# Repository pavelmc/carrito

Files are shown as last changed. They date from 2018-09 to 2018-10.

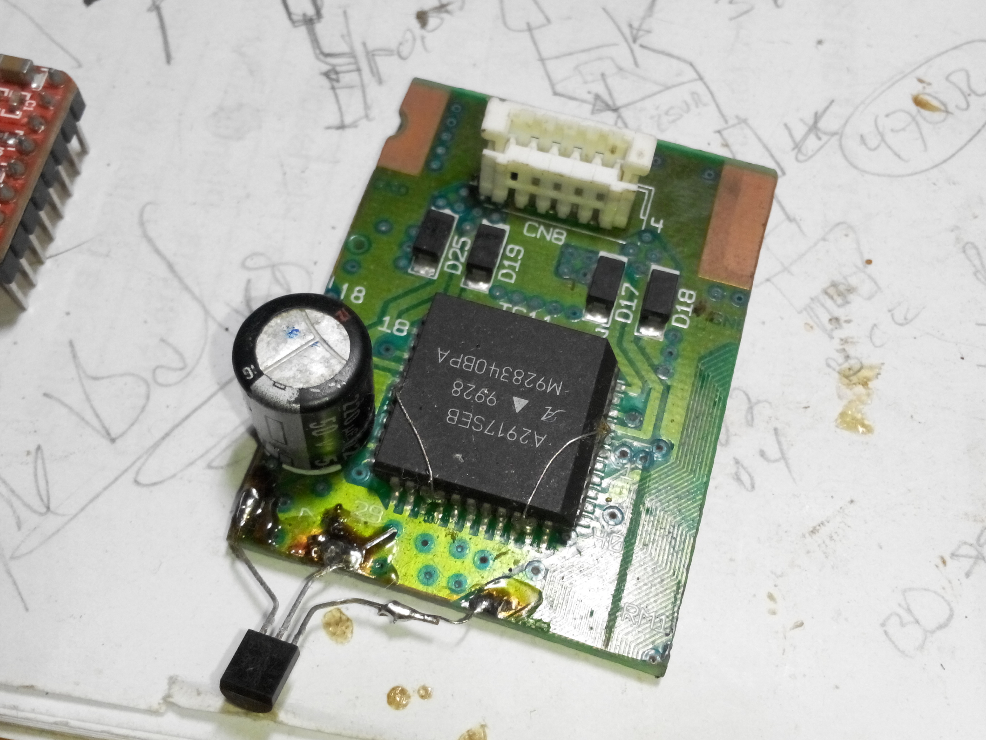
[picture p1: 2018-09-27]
photos/allegro-controller-death.jpg

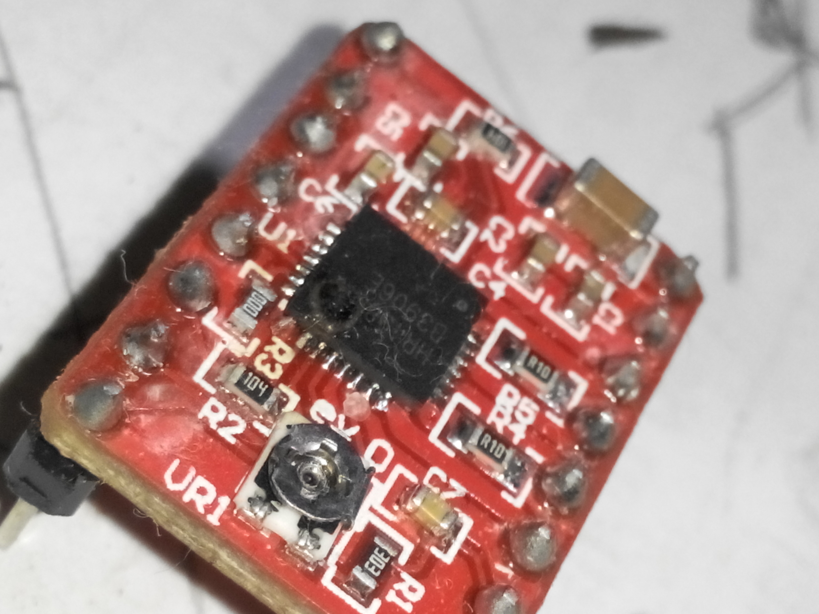
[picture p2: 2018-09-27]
photos/pololu-controller-death.jpg

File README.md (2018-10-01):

# Carrito (Spanish for Small car) #



This is a homebrewed small car powered by Arduino, there is no particular blueprint for it, the parts comes and go to fit my needs, this evolves continually. Almost all parts were scraped from my junkbox.

You can take a peek at the (always evolving) fritzing file in the "extra" directory (there is also PNG and PDF versions for your convenience)

The main motivations to make this car is the fact that I haven't a cool Arduino project to display... I also confess that I didn't had a remote controlled car as a child so I made this to my children also.

# Dependencies #

If you want to build or test this you will need a few extra things not in this repository:

* The [remote control](https://github.com/pavelmc/carrito-control) device to command this thing.
* A custom lib to command the stepper motor, its called [stepperUnipolar](https://github.com/pavelmc/stepperUnipolar) and has some nice features.
* A library to control the nRF24l01 device, I use the nRFLite lib, you can find it on the Arduino IDE Library manager.

# Actual Hardware #

**Power source:** Laptop batteries; I have become a recycle fan of laptop batteries on any kind for many uses, I have it from 1.2Ah to 2.5Ah, in this case I chose 4 cells is 2P2S mode of 2.2Ah, that gives a total of 6.0 to 8.4 V at up to 4.4 Ah, that's plenty of power for the task.

Every lipo battery need a [BMS](wikipedia:battery_monitor_system) and I borrowed one controller from a Baofeng handheld radio battery pack, it was rated 1.800mAh (1,8Ah) but carefully inspection showed that the MOSFET on the BMS was capable of handling up to 10 amps, so it must be up to the task. (I calculate a peak load of 1.3 Amps top)

_note:_ I charged the battery pack at the design stage and after about a month of bench and field test (about 3 to 4 days per week of tests with ~1 hour per day) it's now at ~7.0 V about 50% of charge; maximum current measured was about 1.8A, nice very nice.

**Motion drive:** Old dotmatrix Epson Printer DC motor and gears commanded by a 6AM14 mosfet Bridge that allows to control the direction (polarity inversion) and speed (via a PWM on a P-channel MOSFET)

**Direction control:** Stepper motor controlling a gear that rotates the front wheels. The motor was borrowed from a old dotmatrix Epson Printer. The motor is unipolar (type 17PM-K303, NEMA17 equivalent from Minebea) controlled by 4 MOSFET borrowed from a PC Motherboard (P75N02, 7.5 milli Ohms and 25 Volt) directly connected to the 74HC595 at 0-3.3V logic.

The motor ratings specs 1.2A on the coil and max of 3.0 Volts, so I fit a positive side current limiter using a PNP darlingtown transistor circuit (2SA1568, again borrowed from the printer, this are the pin controllers on the datMatrix printer)

**Direction artifacts:** The front wheels direction has one problem: it can move and miss steps on bumps and hits, so I need some way to know the position, but all time position are good or only a few ones? powering the stepper is a way to keep the direction in place, but that monster eating 1.2 Amp is not an option.

After analyze the situation I found that I will only need three position reports:

* Full left.
* Mid of front facing.
* Full right.

Left/Right limits was implemented with mouse click switches and also served as hardware limiters, the front facing position as a little tricky (I tried some dancing switches from an old bubblejet printer and other options).

I ended with an Hall effect sensor, it has A42E label but I can't find the datasheet _(if you know what part it's I will appreciate any clue, the initial "A" letter seems like the Allegro one)_, it was borrowed from an old floppy disk drive, per the circuit I can tell that it needs a pull up 10k transistor for 5V and of curse the pinout is evident.



This hall sensor triggers a pin low once the direction is facing forward, as simple as that. The pull up is by software on the arduino programming, test proved that it works just fine on 3.3V.

**Remote control:** the remote control is designed/made from day one using a pair of nRF24L01 modules at 250 kbps, more than the needed for the task. I tested a lot of libs for this modules and ended using the nrflite one by his final small size firmware and easy programming.

# No Go Hardware & Failed tries #

This is a list of failed tries of hardware and ideas and his explanation (you can find images of the items described here in the folder no-go-and-failures)

## Power inversion for the power motor ##

First try was using 12V Relays from a UPS, it consumes only 28mA to drive the coil and can handle up to 10A, driver circuit is just a transistor connected to the Arduino, so it was a nice idea, but not in practice.



Theory some times is ridiculously killed by practice: the 8.4V of power was just enough to activate the 12V relays, but once the voltage of the battery dropped to ~7V it's stops of activate the relays, or activates only one... so no-go on this.

Next obvious solution was a H-Bridge, but P MOSFET transistor are rate here, so I surfed the net and found some clever design using power bipolar transistors and even darlingtons NPN-PNP pairs... hummm printers have that...



Yes, I have them PNP 2SA1568 and NPN 2SD2131, so hands to the bech... the result was a bulk & spider wired H bridge on a large heatsink from a PC power supply, it worked well but also dissipated some heat, losses was about 0.3V on PNP and 0.25V on the NPN side, that at ~700 mA, loses was about half a watt on heat, not bad in paper but the "finger test" was no so, it feels uncomfortably hot at touch.

So big and hot, yet I need a PNP transistor to control the +Vcc with the PWM of the Arduino so more bulk and heat, no thanks... I need another solution.

"Only archives a goal who seek and work for it", tells a Spanish old saying. Searching on the junk box I found a old and dust power chip with his original heatsink: 6AM14 Bingo!

That is just 3 pairs of N and P channel matched MOSFETS (7 Amps One and a half H-bridge) so I can wire the H-bridge and the remaining P-channel mosfet to control the PWM, results: under 1mA on standby and losses are under 100mW on work at 1A (no perceptible warm on full power drive), Wow MOSFET RULEZ!!!

## Too big power motor: ##



I prepared the chassis to hold a power motor that is just too big to power this little monster, it eat around 1A at 8.4V and can develop a lot of speed, in the first tries I realized that and discarded it in favor of a motor half the size of that; now it eats 600mA (0.6A) at full power and plenty of speed and power for the task

## Direction Stepper motor to small ##



I build the direction mechanism like an old car, moving the entire front wheels support and not each front wheel at a time in opposite direction (like any modern car). But tests showed that the selected motor (no branding or data, just a unipolar stepper motor of 200 steps per turn, see picture) was not enough for the task at least at 6-8V of power supply with current limiting.

I then moved to another stepper motor bigger and it happens to has a gear that is the same tooth pace that the main gear, this motor was from a Epson printer (is states in the chassis: EM-242) and its of bipolar type.

## Direction stepper motor controller death ##



When I selected the above mentioned bipolar stepper motor I realize that I don't have a bipolar controller, then turned into the printer where it was borrowed and spotted a Allegro controller for it (A2917SEB) I get a hand saw and cut the PCB and by the datasheet I make it and get some code to get it to work.

Early test showed that the main Vcc of the motor was not enough for the task (it works on a +35V Vcc system and I have 6.0 to 8.4V from lipo batteries) I think on ways to increase the power adding more batteries up to 9.0 to 12.6V but that will nedd a BMS of three batteries and I have only 2S BMS at hand.

Testing other tricks I made a wrong connection and... it stopped working: R.I.P. A2917SEB. :(

## Direction stepper motor controller death (yes, the second one) ##

Then I was forced to buy a controller, in the cuban market this is hard but fortunately I found a friend that has a A4899 Pololu controller available, just great!

Buy, mount, test: OK. It works flawlessly, on the test bench. Now it's time to put it on the real hardware... fail... what's wrong? Simple: I switched the motor power (8.4V) with the digital power (max 5.5V)... results: Pololu controller is death, you can see the burn blob on the IC.



Miraculously the Arduino Pro Mini survived!, it received the +8.4V (capable of 4.4 Amps!) and did not die... thanks to the luck I had the nRF24 module disconnected from the Arduino...

This lead to discard the mentioned bipolar motor (I'm mad at bipolar motors... GGGRRR) and switch to the actual unipolar motor with a combination of Mosfets switching the motor coils to ground and a PNP bipolar transistor as current source (1.2 A as per the motor datasheet)

The motor was again borrowed from the same printer, (MINEBEA or MNB brand, type 17PM-K303, and equivalent of a NEMA17 one) datasheet specs are 1.2A current and max 3.0V so my 6.0-8.4V is enough.

## Not enough input/output pins, the case of the 74HC595 ##

At some point I realized that I will have not enough input/output pins, and realizing that I have the hardware SPI bus on use I it to command a 74HC595 shift register.

Then I realize that I will need a way to move the motor pins to the shift register, there is some examples out there, even adafruit has a shield based on that idea, but I can find a lib to make this... so...

I crafted a unipolar stepper lib to address simple pins handling or returning the pin values to pass to a shift register like the 74HC595, you can find it here [stepperunipolar](http://github.com/pavelmc/stepperunipolar) it is on a dev stage, it need a lot of work on the examples and docs to get ready for the public domain, so use it at your own risk.

Still in construction, check back later.

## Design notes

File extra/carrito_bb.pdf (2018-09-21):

6.0v to 8.4V From a
2P2S Lithium Ion
Battery with a
proper BMS

This is a basic Current Source to feed the Stepper motor, in this case 1.2 Amps aprox.

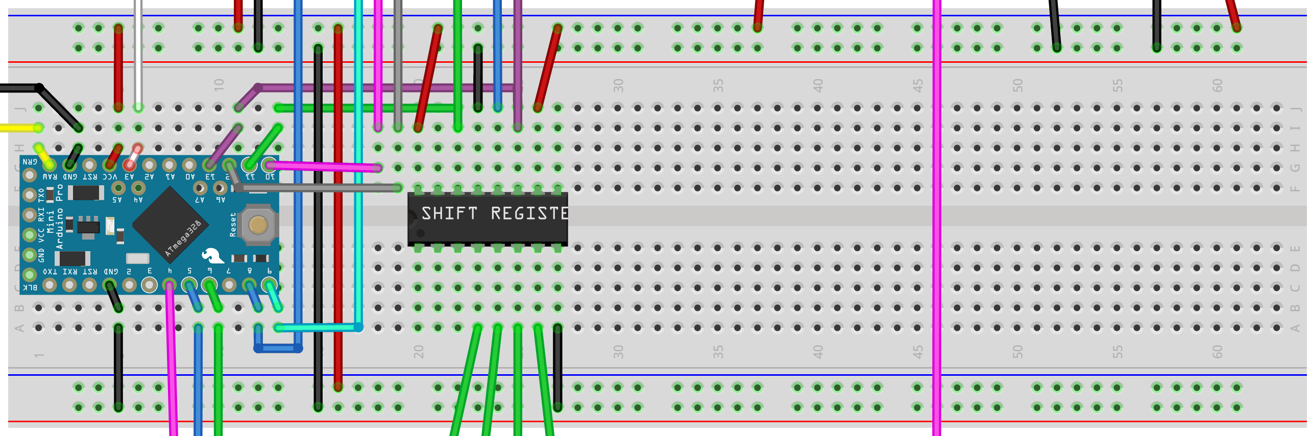
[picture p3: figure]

A Heat Sink is mandatory

Power Transistor is 2SA1568 Lower Power one is 2N3906

This is the motor that turns the front wheels. It's a NEMA17 like 3V@1.2A Unipolar one. Brand is MINEBEA (MNB)

Al 4 N-channel MosFET
are PL06N03 SMD ones
nRF24L01 Module | Two momentary limit switch (the positive feed is the one at the right, the negative feeded is at left)
| One Hall sensor to sign we are facing ahead (it's pulled down when magnet is on position, high the rest of the time)

H-bridge connector + Speed control.

The function is as follow:
* Pin 5 controls the car
movement direction (low
forward, hig reverse)

* Pin 6 is a PWM control of the speed of the movement (with a P-channel MosFET) 0 is no movement and 255 is full
power, Positive going PWM.

Carrito: A remote controlled car from parts in my junkbox =================================================

Author: Pavel Milanes (CO7WT)
E-mail: pavelmc@gmail.com
Web: https://github.com/pavelmc/carrito

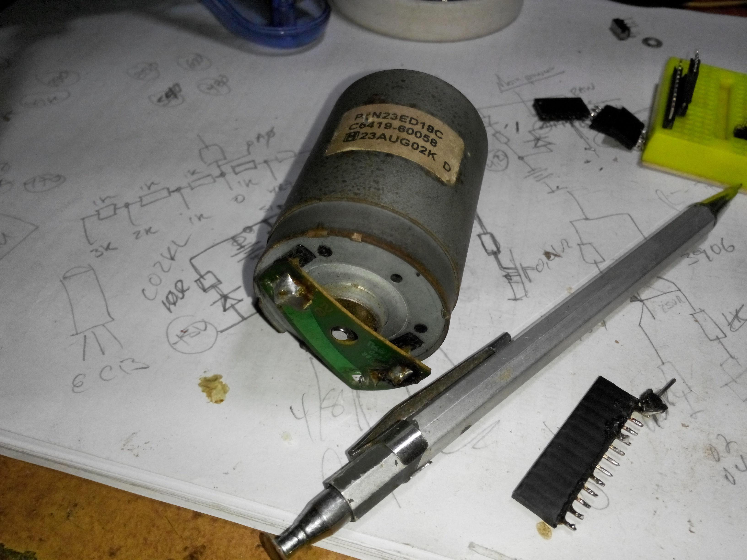
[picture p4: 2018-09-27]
photos/big-motor.jpg

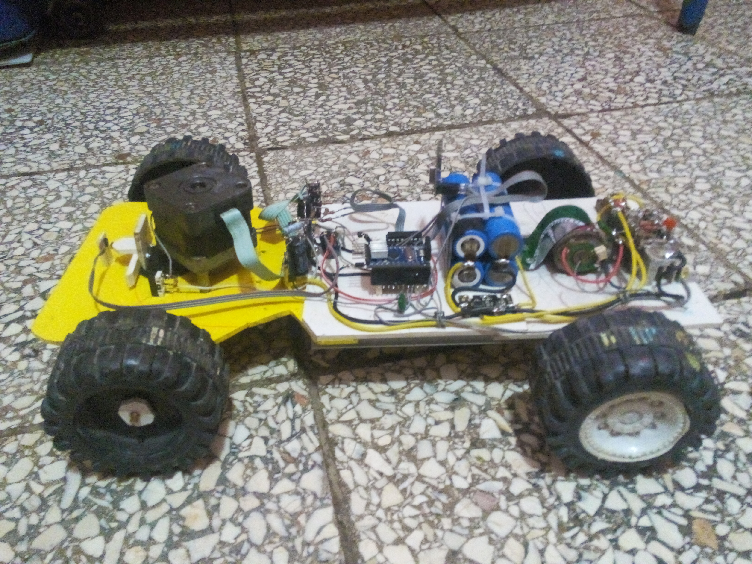
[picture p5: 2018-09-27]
photos/bare-bones-car.jpg

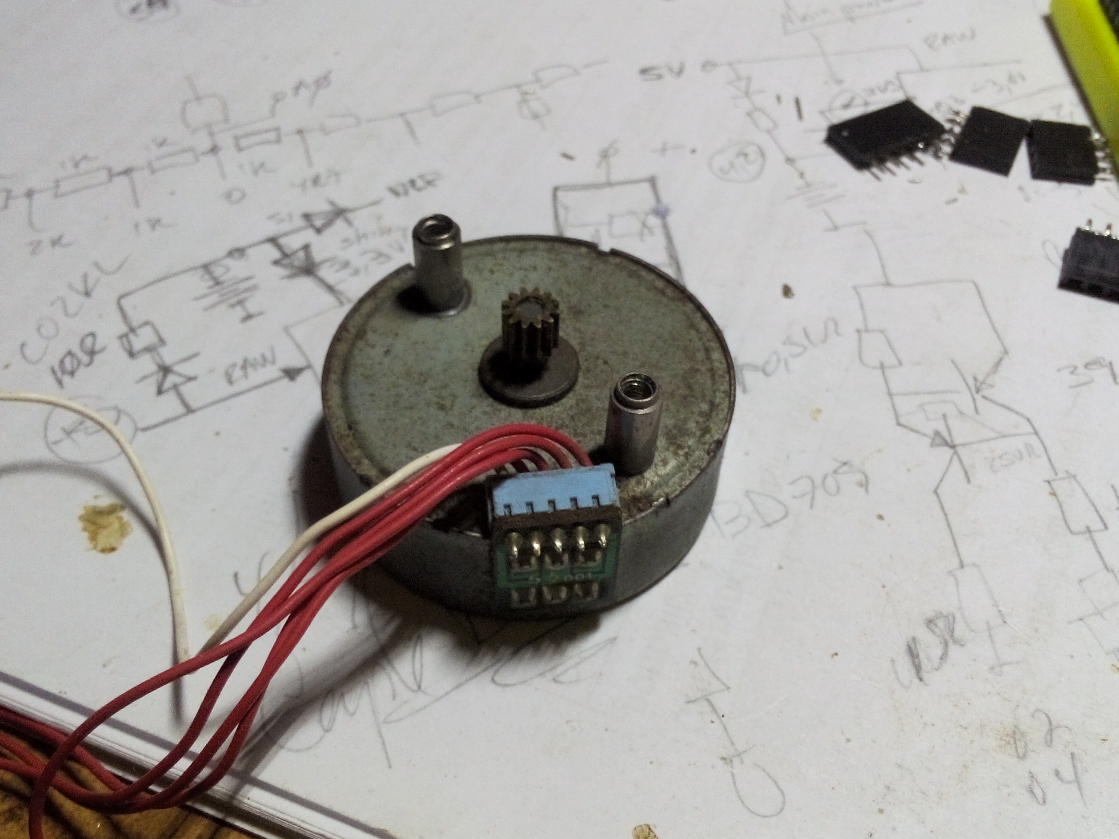
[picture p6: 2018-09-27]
photos/small-stepper-motor.jpg

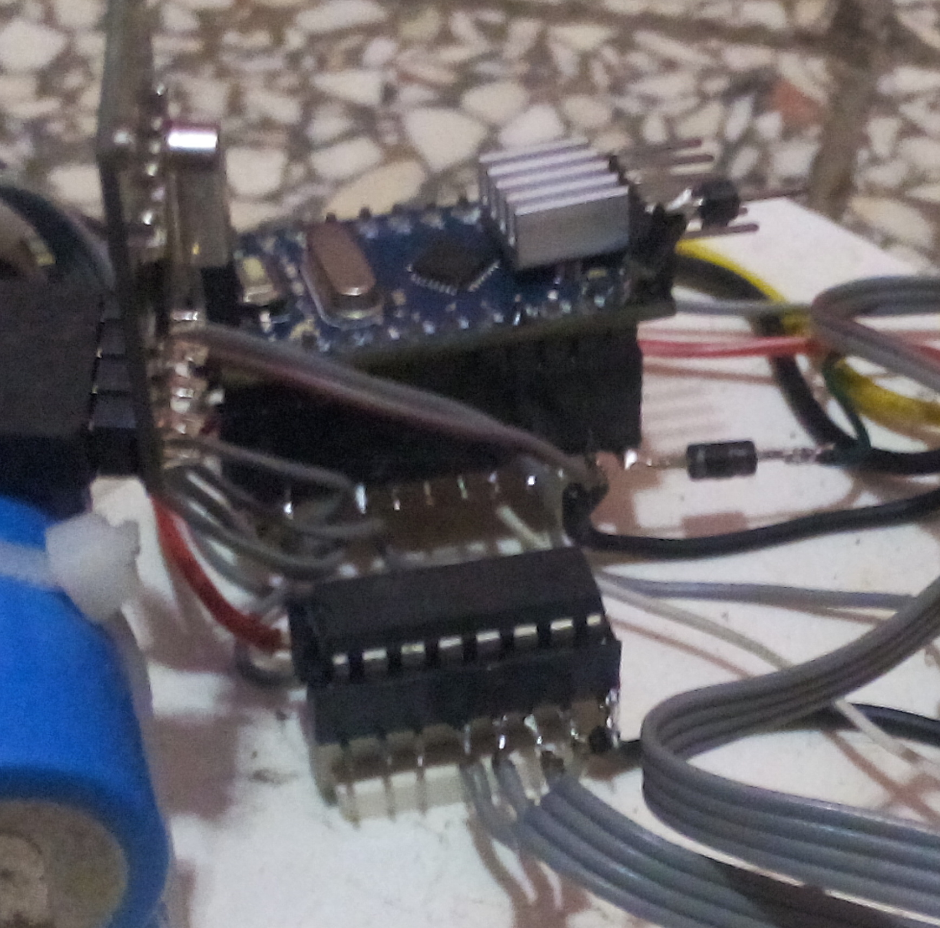
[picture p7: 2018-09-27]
photos/74HC595.jpg

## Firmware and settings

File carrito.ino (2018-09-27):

/*
 * Pin mapping
 *
 * *** NRF24L01 Radio ***
 * Radio    Arduino
 * CE    -> 9
 * CSN   -> 10 (Hardware SPI SS)
 * MOSI  -> 11 (Hardware SPI MOSI)
 * MISO  -> 12 (Hardware SPI MISO)
 * SCK   -> 13 (Hardware SPI SCK)
 * IRQ   -> No connection
 * VCC   -> No more than 3.6 volts
 * GND   -> GND
 *
 * *** DIRECTION MOTOR ***
 * pushed via SPI to the 74HC595 on the upper nibble but is uses ...
 * 8 - as SPI CS for the shift register
 *
 * *** POWER MOTOR ***
 * 6 - PWM motor speed
 * 5 - motor direction (low forward, high reverse)
 *
 * *** DIRECTION LIMIT SWITCHES ***
 * A0 - will float in 1/2 V
 * and will fire 0 or 1023 on each switch hit
 *
 * ** CENTER HALL sensor***
 * 2 - Will be low when direction is centered
 *
 * *** ULTRASONIC RADAR ***
 * 5 - trigger
 * 6 - Echo
 *
 */

//~ /***** SONAR *****/
//~ #include <HCSR04.h>
//~ UltraSonicDistanceSensor distanceSensor(5, 6);

/***** NRF24L01 *****/
#include <SPI.h>
#include <NRFLite.h>

// Our radio's id.  The transmitter will send to this id.
const static uint8_t RADIO_ID = 18;
const static uint8_t PIN_RADIO_CE = 9;
const static uint8_t PIN_RADIO_CSN = 10;

/*************************************************************************
 * Radio data structure explained:
 *
 * We will pass just relative values, aka, increments
 *
 * -> Speed: (int16)
 *      motor speed increments, every tap increment it in a fixed val
 *      the same for decrements
 * -> Speed hold (bool)
 *      true if we are holding the actual speed, false if we must set
 *      the motor free (this means that we keep the FWD/REV key pressed)
 * -> Turn: (int16)
 *      Turn direction increments, every tap increment it in a fixed val
 *      the same for decrements
 * -> Turn hold (bool)
 *      True if we are holding any direction key.
 * -> Options; (unsigned long)
 *      really 4 bytes, first one is bit mapped to options as
 *      lights, siren, etc... the others will be worked out
*************************************************************************/
// Any packet up to 32 bytes can be sent.
struct RadioPacket {
    unsigned long serial = 0;
    int speed;
    bool speed_hold;
    int turn;
    bool turn_hold;
    bool stop = 0;
    bool lookAhead = 0;
    unsigned long options;
};

// instantiate
NRFLite _radio;
RadioPacket _radioData;

/***** Stepper motor *****/

#include "stepperunipolar.h"
// instantiate it using
stepperunipolar dirMot(UNIPOLAR_WAVE);


/************************************************************************/

// constants
#define motorSpeedPin     (6)       // pin that will be controlling the
                                    // PWM speed of the motor
#define motorDirectionPin (5)       // set the direction of rotation
#define maxSpeed          (255)     // maximum speed
#define dirLimitPin       (A3)      // Analog pin for limit switches
#define dirHall           (2)       // pin in wich is the front hall
#define dirLatch          (8)       // latch or CS for the shift register

// Variables
volatile bool center = false; // changed by an interrupt, must be reset after read high
unsigned long pktSerial = 0; // serial to sign for duplicated packets
int speed = 0;               // will be mapped from -255 to 0-255
int turn = 0;                // this will be steps in each direction

bool direction = 0;         // 0 is forward, 1 is backwards
float wallDistance = -1.0;  // distance measured from the sensor
                            // to the wall

byte shiftOptions = 0;      // shift register options, you can only set
                            // the lower four, the upper four are the
                            // direction motor control bits

// Serial DEBUG
//~ #define SDEBUG      0

/************************************************************************/

// interrupt rutine
void centerHit() {
    center = true;
}

// set motion speed, just set the PWM value against the limit
void setSpeed(int val) {
    // local var
    byte lval = byte(abs(val));

    // set global var value
    byte lspeed = map(lval, 0, 255, 0, maxSpeed);

    // apply
    analogWrite(motorSpeedPin, lspeed);
}


// set direction of rotatio of the power motor
// 0 is forward, 1 is back
void setDirection(bool dir) {
    // set global var
    direction = dir;
    // apply
    digitalWrite(motorDirectionPin, direction);
}


// stop motion of the motor
void motionStop() {
    // invert the motor direction for a brief time
    // keep the speed
    setDirection(!direction);

    // delay proportional to the speed
    delay(abs(speed));

    // stop the motor, stop speed
    speed = 0;
    // the increment factor depends on inertia and hance on the weight
    // of the car, you must tweak it to suit your needs, mine in
    // bare-bones is about 5, with full chassis must be higher
    setSpeed(abs(speed) * 5);
}

// do turns
void doturn(int t) {
    /** turn only in possible directions **/
    int lPos = checkLimit();

    // hit right and commanded right, not possible
    if (lPos == 1 and t > 0) return;

    // hit left and commanded left, not possible
    if (lPos == -1 and t < 0) return;

    // middle position, do move to either way
    turn = t;
    dirMot.steps(turn);
}


// receive data from the remote control unit
void rxCommand() {
    // data will be set into a buffer and process flag will be rised

    // receive radio data
    while (_radio.hasData()) {
        // Note how '&' must be placed in front of the variable name.
        _radio.readData(&_radioData);

        // reset the serial
        pktSerial = _radioData.serial;

        /**** priority commands first and will exit the loop ****/

        // Stop
        if (_radioData.stop) {
            // stop motor
            motionStop();

            // exit loop
            break;
        }


        /**** normal commands   ****/

        // look ahead
        if (_radioData.lookAhead) {
            // call the procedure tolookahead
            dirTofont();
            // exit loop
            break;
        }

        // set speed to this
        if (_radioData.speed != 0) {
            // calc speed
            speed += _radioData.speed;

            // check limits
            if (speed < -255) speed = -255;
            if (speed > 255) speed = 255;

            // which direction
            if (speed > 0) {
                // forward
                setDirection(0);
            } else {
                // reverse
                setDirection(1);
            }

            // set speed
            setSpeed(speed);
        }

        // set turn direction
        if (_radioData.turn != 0) {
            // doturn
            doturn(_radioData.turn);
        }

        // set options to this
        //~ setOptions(_radioData.options);

        // DEBUG
        #ifdef SDEBUG
        Serial.println(speed);
        Serial.println(direction);
        #endif
    }
}


// check direction limit switches
char checkLimit() {
    // measure value
    int ana = analogRead(dirLimitPin);

    // check limits
    if (ana < 200) return -1;   // left
    if (ana > 823) return  1;   // right

    // if not in range just return zero
    return 0;
}


// Move direction to the front position
void dirTofont() {
    // check if we are already looking forward
    if (digitalRead(dirHall) == 0) return;

    // local var to set the direction
    int steps = 500;
    if (turn > 0) steps = -500;

    // move
    doturn(steps);

    // move to center
    while(!center) {
        // motor move
        dirMot.check();

        // check limit hit
        if (checkLimit() > 0) {
            // right limit hit, move left
            doturn(-500);
        }

        // check limit hit
        if (checkLimit() < 0) {
            // left limit hit, move right
            doturn(500);
        }
    }

    // reset the center flag
    dirMot.stop();
    center = false;

    // once done reset turn to center
    turn = 0;
}


// shift out the motor data for the direction
void dirShiftOut(byte dat) {
    // move the bits to the upper four and mask it with the shiftOptions
    dat = dat << 4;
    shiftOptions = (shiftOptions & B00001111) + dat;

    // shift it out
    shiftOut();
}


// shift the motor and options out
void shiftOut() {
    // pull the CS low
    digitalWrite(dirLatch, LOW);
    // push it
    SPI.transfer(shiftOptions);
    // pull the CS high
    digitalWrite(dirLatch, HIGH);
}

/************************************************************************/

void setup () {
    // serial console
    #ifdef SDEBUG
    Serial.begin(9600);
    #endif

    // init the NRF radio
    /*****
     * By default, 'init' configures the radio to use a 2MBPS bitrate
     * on channel 100 (channels 0-125 are valid).
     *
     * Both the RX and TX radios must have the same bitrate and
     * channel to communicate with each other.
     *
     * You can assign a different bitrate and channel as shown
     * below.
     *
     * _radio.init(RADIO_ID, PIN_RADIO_CE, PIN_RADIO_CSN,
     *             NRFLite::BITRATE250KBPS, 0)
     * _radio.init(RADIO_ID, PIN_RADIO_CE, PIN_RADIO_CSN,
     *             NRFLite::BITRATE1MBPS, 75)
     * _radio.init(RADIO_ID, PIN_RADIO_CE, PIN_RADIO_CSN,
     *             NRFLite::BITRATE2MBPS, 100)
     *******/
    if (!_radio.init(RADIO_ID, PIN_RADIO_CE, PIN_RADIO_CSN, NRFLite::BITRATE250KBPS, 52)) {
        #ifdef SDEBUG
        Serial.println("Cannot communicate with radio");
        #endif
        while (1); // Wait here forever.
    }

    // Radio initialized ok
    #ifdef SDEBUG
    Serial.println("Radio init done.");
    #endif

    // direction motor
    pinMode(dirLatch, OUTPUT);
    digitalWrite(dirLatch, HIGH);
    // set call back function
    dirMot.addCallBack(dirShiftOut);
    // set speed in steps per one second (1000 Max)
    dirMot.speed(80);
    // set steps per turn
    dirMot.stepsPerTurn = 200;
    // set eco mode, just power during the move, on idle poweroff
    dirMot.eco = true;

    // hal sensor setup (FALLING, it's normally high)
    pinMode(dirHall, INPUT_PULLUP);
    attachInterrupt(digitalPinToInterrupt(dirHall), centerHit, FALLING);

    // delay to allow for settling.
    delay(500);

    // face fwd
    dirTofont();

    // set pins related to FWD/REV and speed
    pinMode(motorSpeedPin, OUTPUT);
    pinMode(motorDirectionPin, OUTPUT);

}


void loop () {
    // Every 500 miliseconds, do a measurement using the sensor and print the distance in centimeters.
    //~ #ifdef SDEBUG
    //~ Serial.println(distanceSensor.measureDistanceCm());
    //~ #endif
    //~ delay(500);

    // receive data from remote control
    rxCommand();

    // check async to do the move
    dirMot.check();
}

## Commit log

2018-09-08 Include Debug and Fix the bug of reverse values of speed
    [carrito.ino]
2018-09-21 Lot of changes: Hall center became a ISR, improved the stop procedure, improved the turn procedure, improved the dir to front procedure
2018-09-21 Add schematic files
    [carrito.fzz]
2018-09-27 Disable sonar lib, not yet implemented
